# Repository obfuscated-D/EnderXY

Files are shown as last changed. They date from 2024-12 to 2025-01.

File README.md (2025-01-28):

# Ender3XY Conversion

# NOTE: I will be adding more information and resources as I go.All the files and designs are here but assembly instructions are not finished. Unfortunately I don't have as much free time as I did when I started this project.

<p align="center">
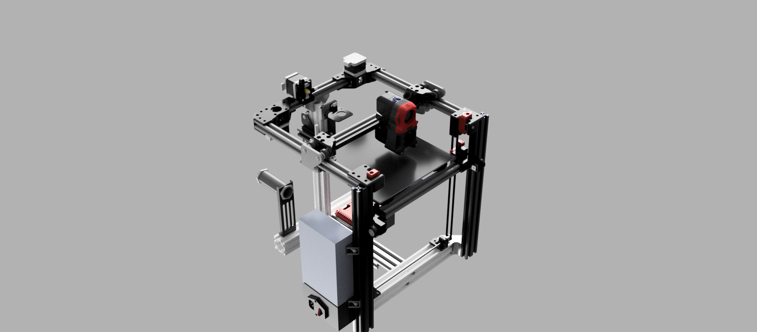
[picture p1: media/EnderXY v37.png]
enderxy

</p>

## Please Read Everything Below Before Contributing, Commenting, or Opening Issues, Thank You!
### This isn't a finished product / refined design. This was a *very* quick concept build and could absolutely use improvement. I hope it can serve as a decent starting point.

# Disclaimer
This project is not affiliated with Creality, Voron Design, Marlin, Mainsail, Klipper, or any other company or project. This is a personal project, and is not intended to be sold or distributed for profit. This project is provided as-is, and I am not responsible for any damage to your printer, or any other equipment. Please accept that when you start this conversion, you cannot change the printer back to stock. By using this project, you agree to take full responsibility for any damage or injury that may occur.

## Skill Level
This project is not for beginners. You should have a good understanding of 3D printing, and be comfortable with modifying and assembling a 3D printer (including drilling, cutting and tapping metal, soldering, etc.). You should also be comfortable with flashing firmware, and configuring it.

# Ender3XY
This is a project to convert a Creality Ender 3 into a CoreXY printer. The goal is to make a good, fast printer from a cheap, slow printer.
- [Contributing](#contributing)
- [TODO's and notes](#todos-and-notes)
- [Klipper](#klipper)
- [Marlin](#marlin)
# Goals
- Make a good printer from a cheap printer
- Keep part cost under $50usd for the conversion
- Use as many stock parts as possible
- Make it easily upgradeable
- Make it easily printable
- Make it easily assembled
- Make it easily sourced

## Print specs
So far, on the bone stock conversion, I can reliably print very good quality at 10k acceleration, and around 120mm/s with a .2 layer height. The mk8 extruder really maxes out around 10mm/s^3.

## Specs
Build volume (X,Y,Z):

 200,185,200           

## Cost
This will vary wildly with person and location. It's reasonable to assume you can get all the necessary parts for the basic stock conversion (not including the printer), for about $60usd. You'll use a good bit of filament as well.

### The Design
The gantry is an adaptation of a [Voron Trident](https://www.vorondesign.com/voron_trident). Of course, the linear rail version is better, but the V wheel version keeps the cost down, and works great! If you build the v wheel version, you can easily change over to the linear rail version in the future without any modification to the frame or belts. Just attach the rails and swap out the X beam ends.

### The Tool Head
I went with an Afterburner Bowden setup. You can use the afterburner, stealthburner, or dragon burner. The files in here allow you to use the stock ender3 hotend in the afterburner, with a 5015 cooling fan. The 5015 fan upgrade is a must for printing PLA fast. The files for the 5015 fan mod are from [Greg191134](https://github.com/Greg191134/Voron/tree/master/Afterburner%20Optimisation/5015%20fan%20mod).

### Filament Feed
Bowden feed is not the greatest, and is a limiting factor as far as print quality and speed are concerned. The upside of running the Bowden is it greatly decreases the mass fo the gantry. If using the stock motors, this is important! Direct drive would be much better, but wouldn't be worth it without A/B motor upgrades. 

## Marlin Firmware
YOU MAY NEED TO ADJUST SOME OF THE CONFIGURATION !!
In the firmware directory, you will find two .bin files.One for the stm32 and one for the gd32f.  These reflect the configurations found in the marlin configuration files directory. These will only work for:
- Ender3 4.2.2 mainboard with A4988 drivers and stm32 processor
- Ender3 4.2.2 mainboard with A4988 drivers and gd32f processor

### If your board does not match, THE FIRMWARE WILL NOT WORK FOR YOU!
 You need to identify your board and stepper drivers, adjust the configuration files for your build, and build a marlin image. The configuration files needed for marlin 2.x bugfix are in the Marlin_files directory. See [Marlin](https://github.com/MarlinFirmware/Marlin) for more information on how to build your own firmware.

# Klipper
For around $22usd, you can get a raspberry pi zero 2W, and run mainsail with klipper! The Klipper directory has the printer.cfg file for the EnderXY, based on the 4.2.2 mainboard. See [Klipper](https://github.com/Klipper3d/klipper/tree/master) for more info and setup instructions.

# Contributing
I would love to see this project grow, and I would love to see what others can do with it. If you have any ideas, improvements, or requests, please feel free to open an issue, or, fork the project and make a pull request.

# Before you Contribute, Please Read!
### It's easy to just throw money at this, to add better parts and make it a better printer. That's not the point of this project, and it's what makes it a challenge. The point is to make a good printer from a cheap printer, using as many stock parts as possible.
### If you have a suggestion, please consider the cost and the availability of the parts. If you have a design change, please consider the ease of printing and the ease of assembly.
### If you have a request, please consider the goals of the project, and the limitations of the stock parts.

## TODO's and notes
    - optmize part designs for printing without support

# Sources and mentions
The only reason this project was possible, and frankly, why I was able to create the first concept so quickly, is because of awesome open source projects! I don't want anyone to think that I did something amazing here, I simply adapted what I could from others, and made a few parts that weren't out there yet.

Of course [Voron Design](https://vorondesign.com/). An amazing, very generous engineering team.

[Marlin](https://github.com/MarlinFirmware/Marlin), Making the maker world a better place.

This wonderful person [Greg191134](https://github.com/Greg191134) is the source of the 5015 fan mod for the afterburner: [Afterburner 5015 fan mod](https://github.com/Greg191134/Voron/tree/master/Afterburner%20Optimisation/5015%20fan%20mod). They also have an awesome project called the Vorender-4, where they upcycled an ender 4 with an adaptation of the Trident gantry.

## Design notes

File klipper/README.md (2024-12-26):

# Klipper

### The printer.cfg in has been tested with Ender3 4.2.2 mainboard, with the stm32 and gd32f chipsets. 

### There is no guarantee that it will work for you! You may need to modify the printer.cfg once up and running.
### See the [Mainsail docs](https://docs.mainsail.xyz/) for more info on setting up your printer.

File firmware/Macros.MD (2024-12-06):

# Here are some print start and print end macros. You can add this to Machine Settings in Cura
```
; EnderXY Custom Start G-code
G92 E0 ; Reset Extruder
G28 ; Home all axes
G1 Z2.0 F3000 ; Move Z up
G1 X0.1 Y20 Z0.3 F5000.0 ; Move to start position
G1 X0.1 Y150.0 Z0.3 F1500.0 E15 ; Draw the first line
G1 X0.4 Y150.0 Z0.3 F5000.0 ; Move to side a little
G1 X0.4 Y20 Z0.3 F1500.0 E30 ; Draw the second line
G92 E0 ; Reset Extruder
G1 Z2.0 F3000 ; Move Z up
G1 X5 Y20 Z0.3 F5000.0 ; Move over to prevent blob squish
```

```
G91 ;Relative positioning
G1 E-2 F2700 ;Retract a bit
G1 E-2 Z0.2 F2400 ;Retract and raise Z
G1 X5 Y5 F3000 ;Wipe out
G1 Z10 ;Raise Z more
G90 ;Absolute positioning

G1 X0 Y{machine_depth} ;Present print
M106 S0 ;Turn-off fan
M104 S0 ;Turn-off hotend
M140 S0 ;Turn-off bed

M84 X Y E ;Disable all steppers but Z
```

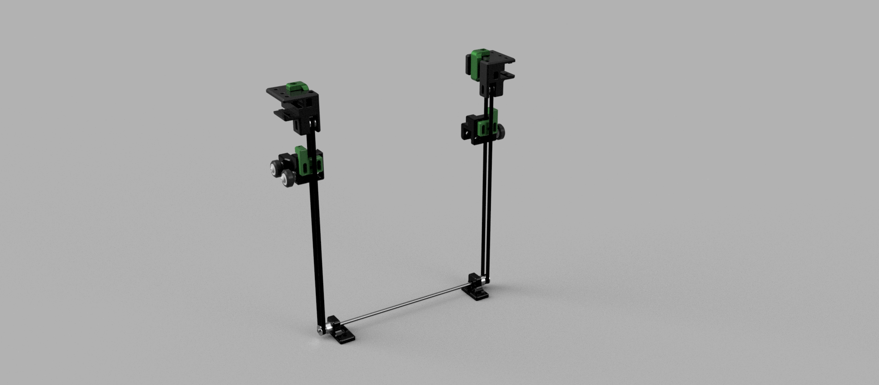
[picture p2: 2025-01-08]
media/Torsion Bar System v7.png

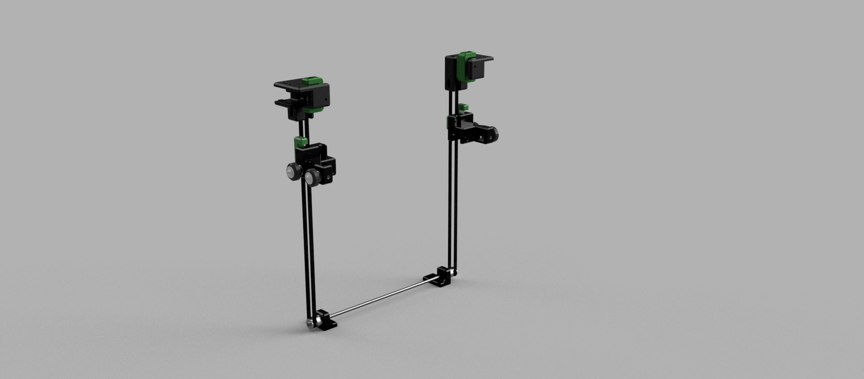
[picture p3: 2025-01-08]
media/Torsion Bar System Front v7.png

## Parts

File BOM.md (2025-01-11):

# The bolt counts are generous, and you may end up with extras
# Extra Components needed to build the EnderXY

        1 Ender-3 printer

## Frame components 
### 20x20 Extrusions:
        1x 196mm
        2x 330mm
        1x 289mm

## Motion Components

        20 F695-2RS Flanged Ball Bearing 5x13x4mm
        
        4 20 Tooth GT2 Idler Pulley, 5mm Bore, 10mm Width 

        2 20 Tooth GT2 Pulley, 5mm Bore, 10mm Width ( 4 if using aftermarket motors!)

        5 meter roll GT2 Timing belt

        250mm mgn12 linear rail (for x axis)
        
        mgn12 linear rail carriage

        300mm 5mm shaft

## Electrical
        For afterburner with 5015 fan:

                1 24V 5015 Blower fan (GDSTIME or SUNON recommended, some cheap fans barely move any air)

        ~5 meters 20 awg wire (for extending the part fan ,motors, and some of the limit switch wires)

        heat shrink for 20 awg wire

## Fasteners

        60 M5x10 BHCS
        
        20 M5x12 BHCS
        
        6 M5x20 BHCS
        
        6 M5x16 BHCS
        
        10 M5x30 BHCS
        
        2 M5x40 BHCS
        
        15 M5x40 SHCS
        
        20 M5 nuts

        30 M5 washers

        100 M5 t-nuts

        8 M3x8 SHCS

        10 M3x12 SHCS

        4 M3x16 BHCS

        4 M3x20 SHCS

        8 M3x25 SHCS

        6 M3x30 SHCS

        8 M3x40 SHCS

        For extrusion with 6mm bolt hole:
                2 M6x20 BHCS 

        For extrusions with 5mm bolt hole:
                2 M5x20 BHCS 

        8  M4 nuts

        16 M3 nuts

        M3x4 heat set inserts (~25)
# Misc
        
        solder
        heat shrink
        zip ties

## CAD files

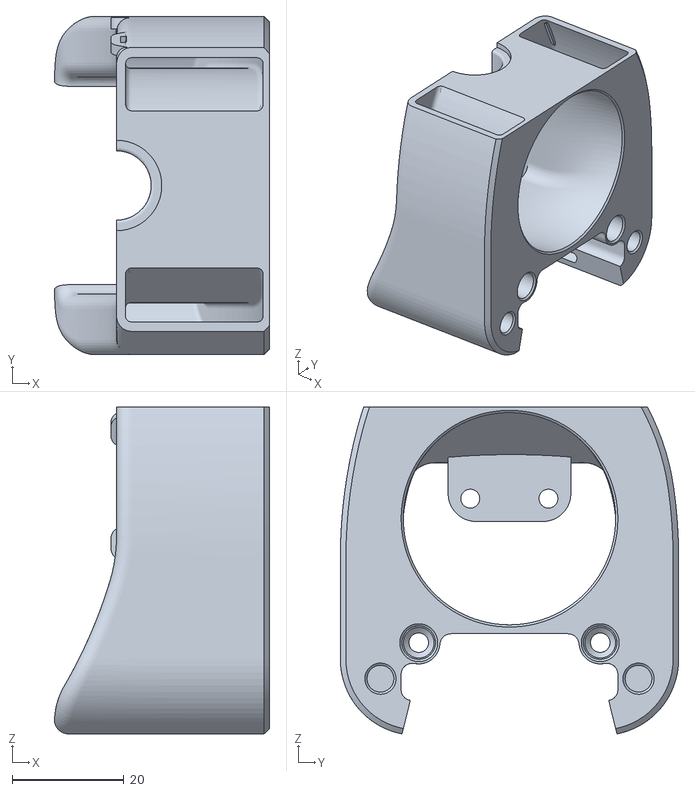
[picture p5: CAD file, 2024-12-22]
STLs/afterburner/mk8-front.stl
38.5 x 60.6 x 58.6

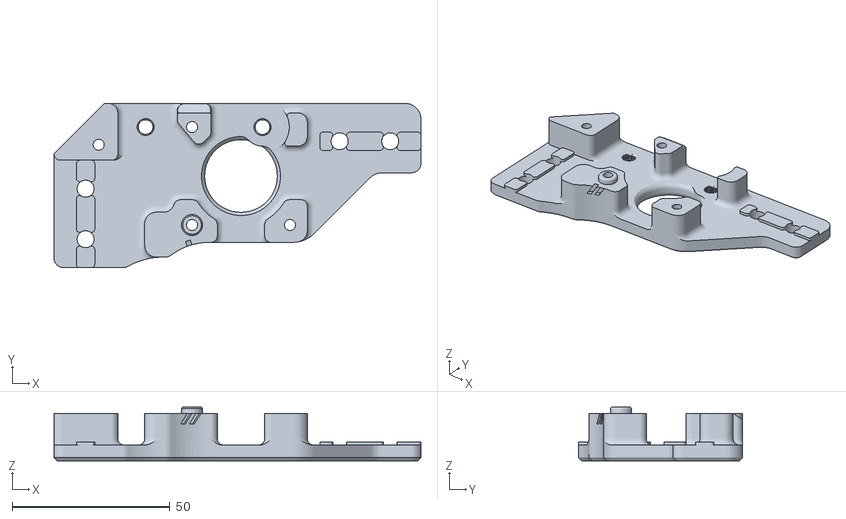
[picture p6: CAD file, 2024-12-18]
STLs/Gantry/Drives/drive_lower_x2.stl
116.2 x 52.0 x 17.0

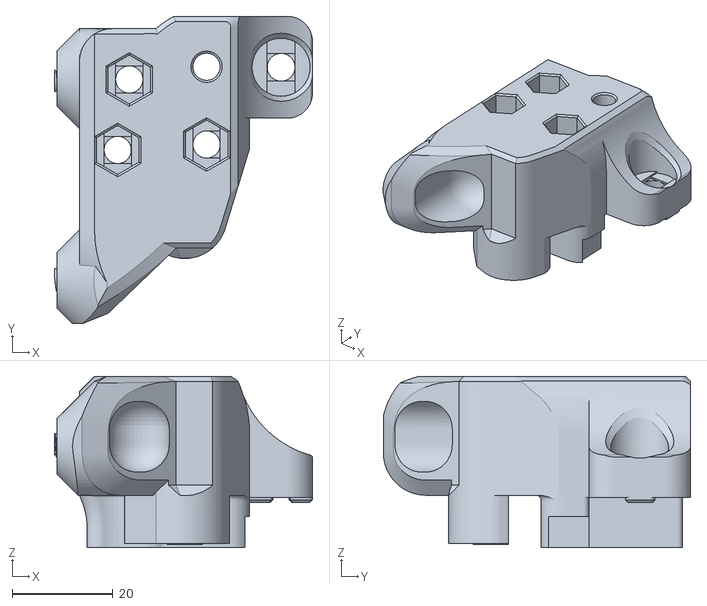
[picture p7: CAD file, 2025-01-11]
STLs/Gantry/x_gantry_end_left_upper_x1.stl
51.2 x 61.0 x 34.0

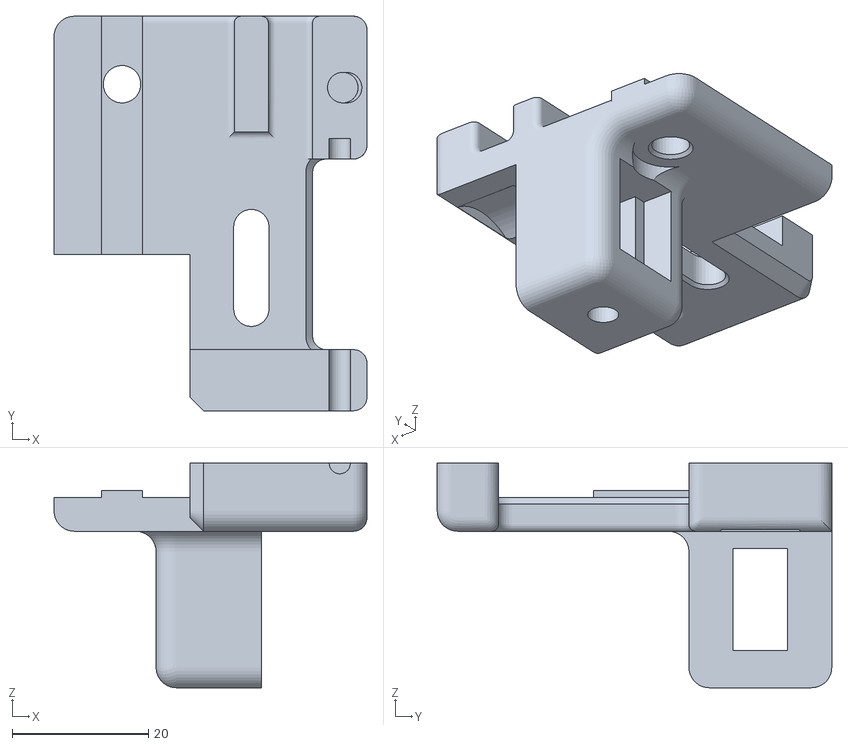
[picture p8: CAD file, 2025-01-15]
STLs/Idlers/idler_b_belted_lower.stl
46.0 x 58.0 x 33.0

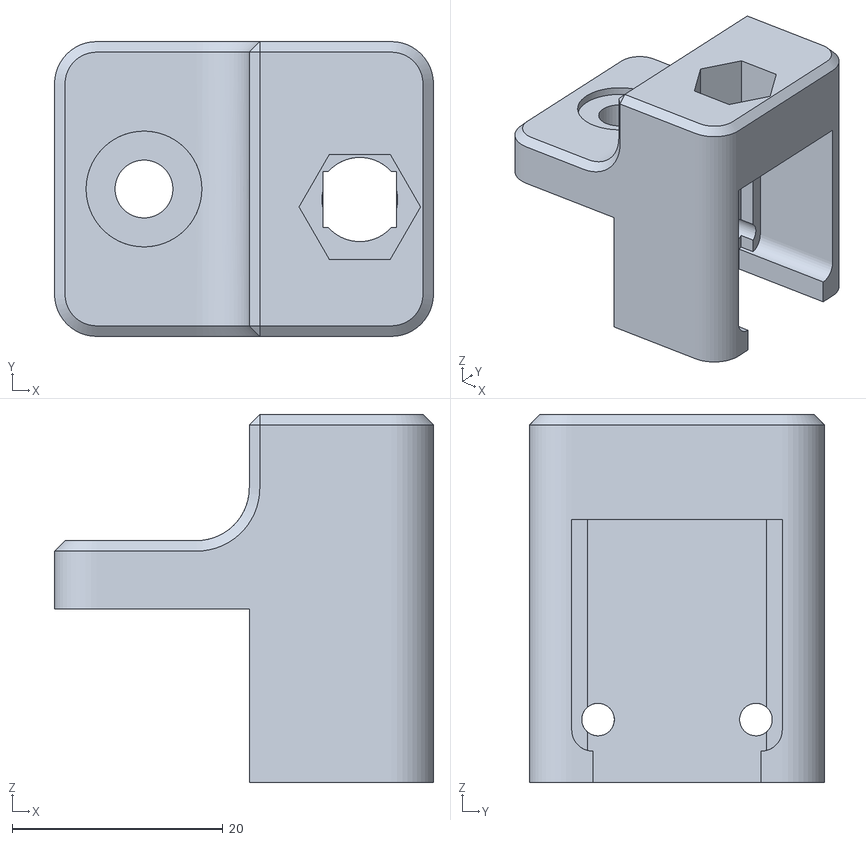
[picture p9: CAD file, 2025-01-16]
STLs/z_endstop_body.stl
36.0 x 28.0 x 35.0

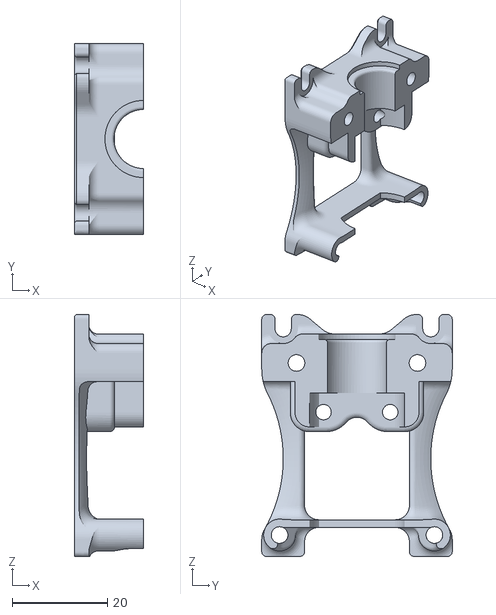
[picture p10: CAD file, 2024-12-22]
STLs/afterburner/mk8-back.stl
14.5 x 40.0 x 50.8

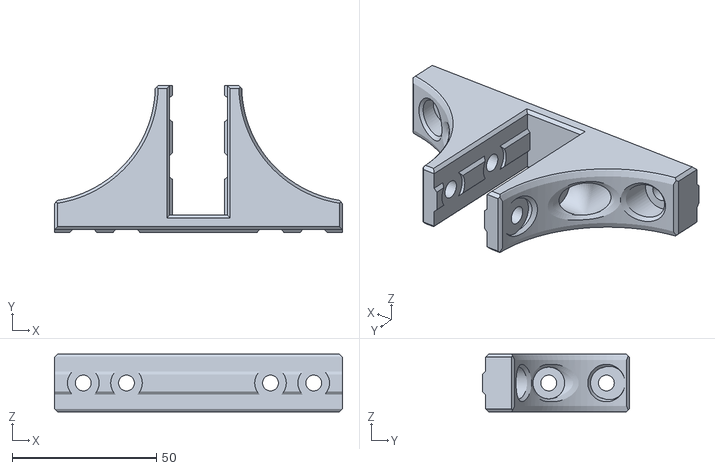
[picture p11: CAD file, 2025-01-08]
STLs/front_support_bracket_x1.stl
100.0 x 51.0 x 20.0

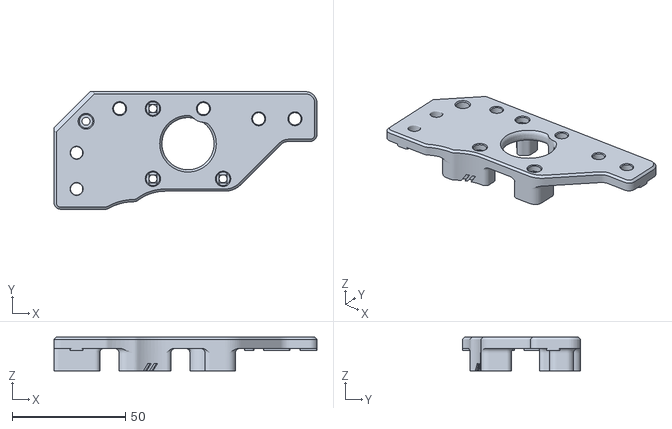
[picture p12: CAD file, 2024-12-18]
STLs/Gantry/Drives/drive_upper_x2.stl
116.2 x 52.0 x 15.0

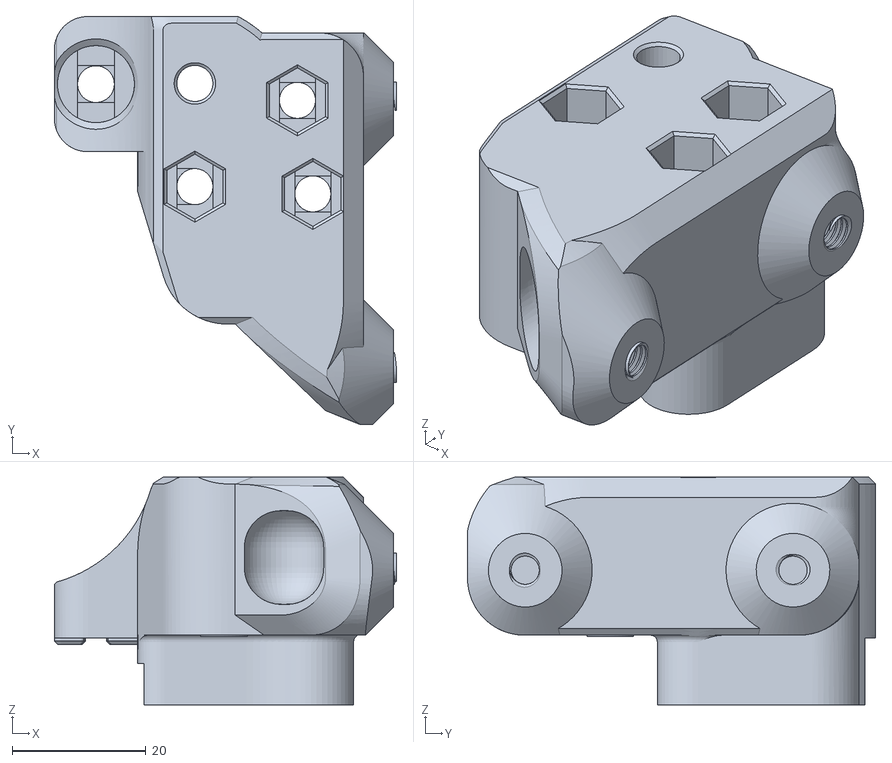
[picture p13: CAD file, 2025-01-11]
STLs/Gantry/x_gantry_end_right_upper_x1.stl
51.2 x 60.9 x 34.0

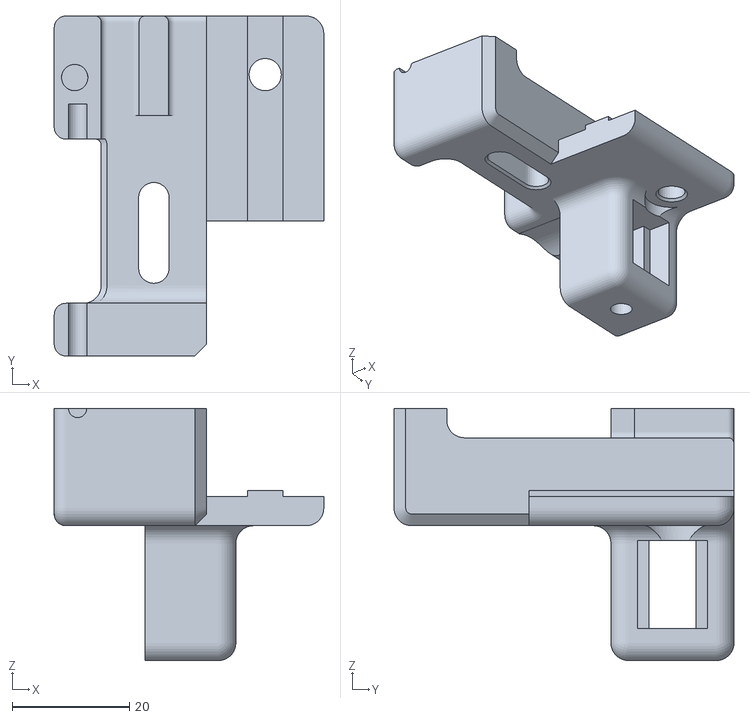
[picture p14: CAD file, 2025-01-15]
STLs/Idlers/ider_a_belted_lower.stl
46.0 x 58.0 x 43.0

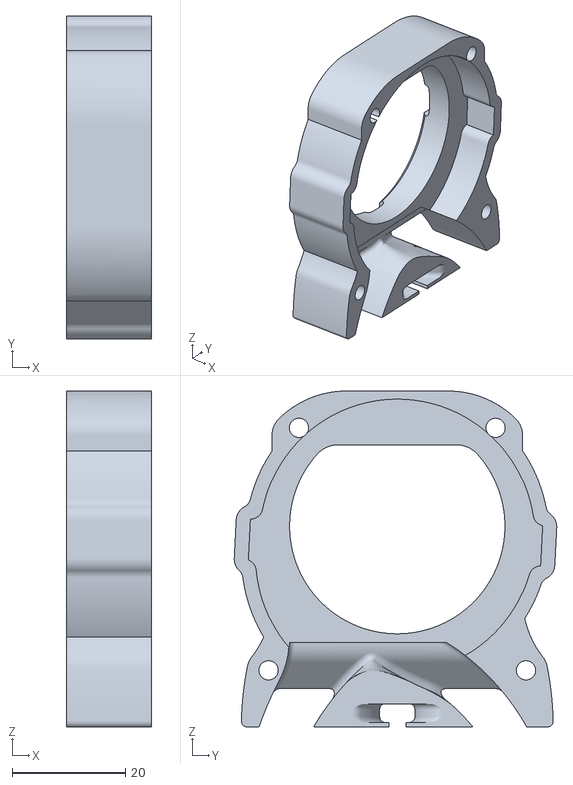
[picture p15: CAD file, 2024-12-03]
STLs/afterburner/5015_mount_back.stl
15.0 x 56.9 x 59.3

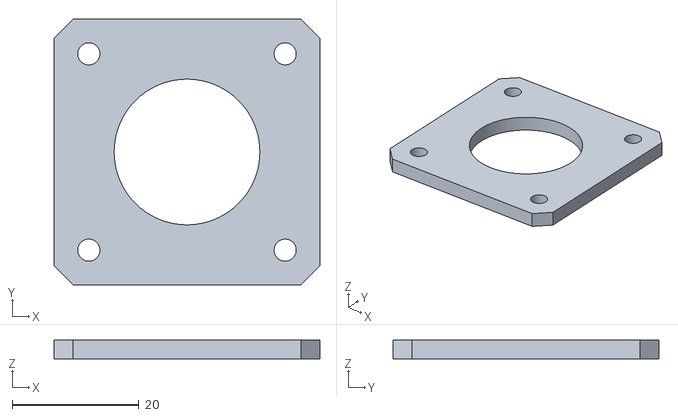
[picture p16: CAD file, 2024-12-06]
STLs/Gantry/Drives/stock_motor_spacer_x2.stl
42.0 x 42.0 x 3.00

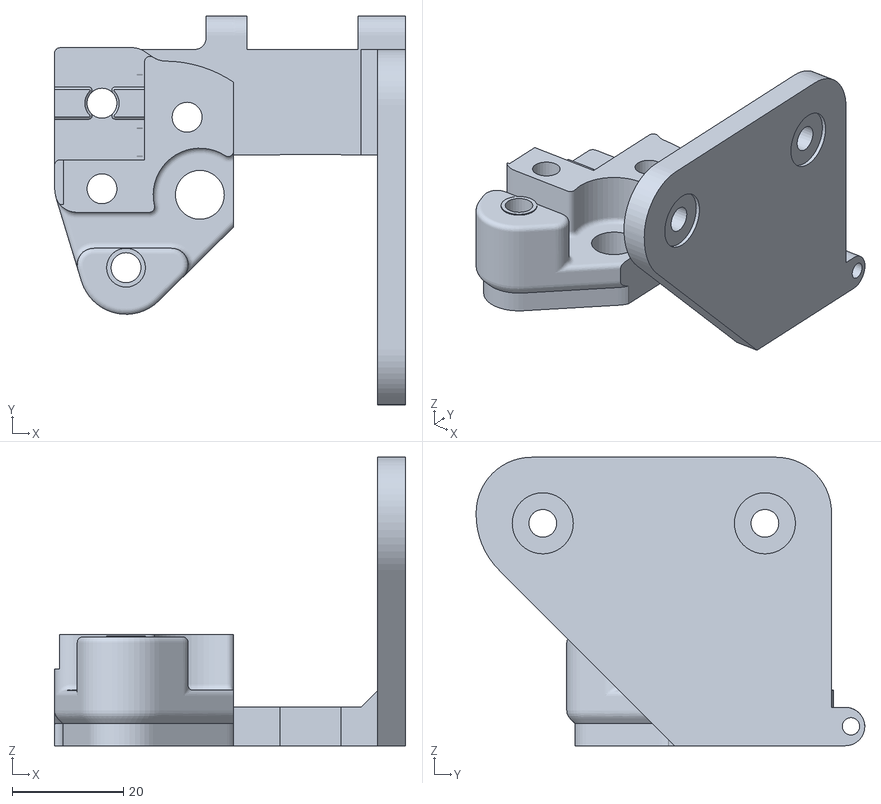
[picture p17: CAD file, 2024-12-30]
STLs/Gantry/x_gantry_end_right_bottom_x1.stl
63.2 x 70.0 x 52.0

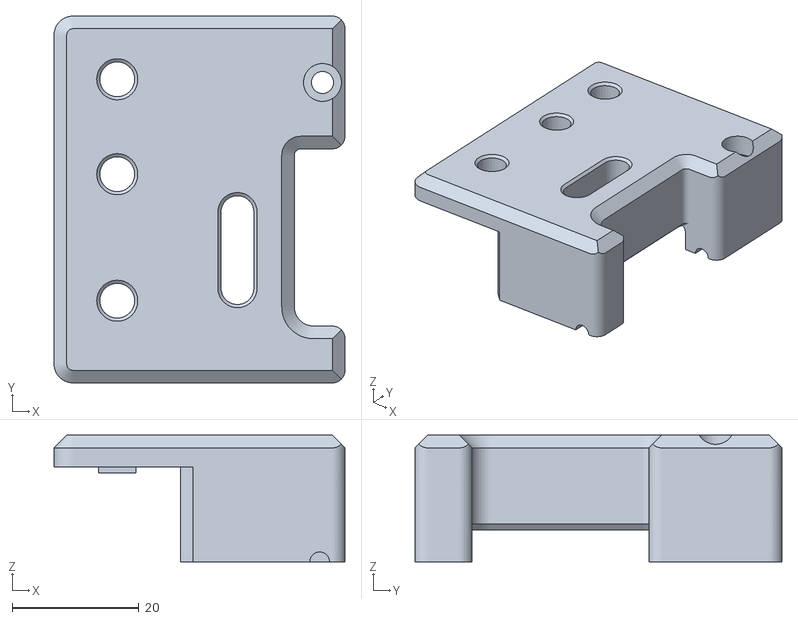
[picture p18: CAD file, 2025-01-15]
STLs/Idlers/idler_b_belted_top.stl
46.0 x 58.0 x 20.0

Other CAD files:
STLs/z_belt_clamp_right_x1.stl
STLs/afterburner/bowden_rear.stl
STLs/Gantry/x_gantry_end_left_bottom_x1.stl
STLs/Gantry/[a]_tensioner_left_x1.stl
STLs/Gantry/[a]_tensioner_right_x1.stl
STLs/Gantry/v_wheel_tensioner_left_x1.stl
STLs/Gantry/v_wheel_tensioner_right_x1.stl
STLs/Gantry/x_carriage_left_x1.stl
STLs/Gantry/x_carriage_right_x1.stl
STLs/Idlers/idler_a_belted_top.stl
STLs/Y_limit_switch_mount_x1.stl
STLs/afterburner/5015_mount_front - Sunon 5015 fan.stl
STLs/afterburner/bowden_single_front.stl
STLs/afterburner/hotend_fan_mount.stl
STLs/bearing_block_left_x1.stl
STLs/bearing_block_right_x1.stl
STLs/electronics_enclosure_bottom.stl
STLs/electronics_enclosure_top.stl
STLs/frame_rear_mount_x1.stl
STLs/front_beam_roller_belted_z_left_x1.stl
STLs/front_beam_roller_belted_z_right_x1.stl
STLs/front_leg_support_left_x1.stl
STLs/front_leg_support_right_x1.stl
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

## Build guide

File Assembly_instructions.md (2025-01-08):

# Required Tools
- Drill (Drill press preferably)
- 5mm (5x.8) tap and appropriate Drill
- 6mm (6x1) tap in some cases and appropriate drill (some available 20mm extrusions have a hole too large for 5mm threads)
- 3mm tap
- Drill
- Drill bit set
- 300mm (12 inch) square
- Allen wrench set (metric)
- Hacksaw (something to cut the extrusions)
- Wiring tools (wire stripper, jst crimpers, wire cutters,etc)
- Soldering Iron
- 3D printer
- Metric ruler and calipers (up to 350mm)
- File
- Sandpaper
- Deburring tool or hobby knife
- Side cutters

## Printing parts:
### Settings:
- ABS or ASA is recommended, but PETG will work (components near the bed and hotend may warp over time if using PETG)
- 0.4mm nozzle
- 0.2mm layer height
- 30% gyroid infill
- 3 perimeters
- 4 top and bottom layers
- Zig Zag support where needed (easier to remove)

- Each component in the STL directory has it's name followed by _x(n), where n is the number of them you need to print. If there is no number, print one.
- Special cases:
    - For the front leg supports, if you are using the stock electronics enclosure, you need to print one left and one right. 
    - If not using the stock enclosure, print 2 lefts

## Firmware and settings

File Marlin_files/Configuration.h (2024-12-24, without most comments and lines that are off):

#pragma once
#define CONFIG_EXAMPLES_DIR "Creality/Ender-3/CrealityV422"
#define CONFIGURATION_H_VERSION 02010300
#define STRING_CONFIG_H_AUTHOR "Obfuscated_D" // Original author or contributor.
  #define MOTHERBOARD BOARD_CREALITY_V422
#define SERIAL_PORT 1
#define BAUDRATE 115200
#define CUSTOM_MACHINE_NAME "EnderXY 0.0.1"
#define X_DRIVER_TYPE  TMC2208_STANDALONE
#define Y_DRIVER_TYPE  TMC2208_STANDALONE
#define Z_DRIVER_TYPE  TMC2208_STANDALONE
#define E0_DRIVER_TYPE TMC2208_STANDALONE
#define EXTRUDERS 1
#define DEFAULT_NOMINAL_FILAMENT_DIA 1.75
#define TEMP_SENSOR_0 1
#define TEMP_SENSOR_1 0
#define TEMP_SENSOR_2 0
#define TEMP_SENSOR_3 0
#define TEMP_SENSOR_4 0
#define TEMP_SENSOR_5 0
#define TEMP_SENSOR_6 0
#define TEMP_SENSOR_7 0
#define TEMP_SENSOR_BED 1
#define TEMP_SENSOR_PROBE 0
#define TEMP_SENSOR_CHAMBER 0
#define TEMP_SENSOR_COOLER 0
#define TEMP_SENSOR_BOARD 0
#define TEMP_SENSOR_SOC 0
#define TEMP_SENSOR_REDUNDANT 0
#define DUMMY_THERMISTOR_998_VALUE  25
#define DUMMY_THERMISTOR_999_VALUE 100
#if TEMP_SENSOR_IS_MAX_TC(0)
  #define MAX31865_SENSOR_OHMS_0      100 // (Ω) Typically 100 or 1000 (PT100 or PT1000)
  #define MAX31865_CALIBRATION_OHMS_0 430 // (Ω) Typically 430 for Adafruit PT100; 4300 for Adafruit PT1000
#endif
#if TEMP_SENSOR_IS_MAX_TC(1)
  #define MAX31865_SENSOR_OHMS_1      100
  #define MAX31865_CALIBRATION_OHMS_1 430
#endif
#if TEMP_SENSOR_IS_MAX_TC(2)
  #define MAX31865_SENSOR_OHMS_2      100
  #define MAX31865_CALIBRATION_OHMS_2 430
#endif
#if HAS_E_TEMP_SENSOR
  #define TEMP_RESIDENCY_TIME         10  // (seconds) Time to wait for hotend to "settle" in M109
  #define TEMP_WINDOW                  1  // (°C) Temperature proximity for the "temperature reached" timer
  #define TEMP_HYSTERESIS              3  // (°C) Temperature proximity considered "close enough" to the target
#endif
#if TEMP_SENSOR_BED
  #define TEMP_BED_RESIDENCY_TIME     10  // (seconds) Time to wait for bed to "settle" in M190
  #define TEMP_BED_WINDOW              1  // (°C) Temperature proximity for the "temperature reached" timer
  #define TEMP_BED_HYSTERESIS          3  // (°C) Temperature proximity considered "close enough" to the target
#endif
#if TEMP_SENSOR_CHAMBER
  #define TEMP_CHAMBER_RESIDENCY_TIME 10  // (seconds) Time to wait for chamber to "settle" in M191
  #define TEMP_CHAMBER_WINDOW          1  // (°C) Temperature proximity for the "temperature reached" timer
  #define TEMP_CHAMBER_HYSTERESIS      3  // (°C) Temperature proximity considered "close enough" to the target
#endif
#if TEMP_SENSOR_REDUNDANT
  #define TEMP_SENSOR_REDUNDANT_SOURCE    E1  // The sensor that will provide the redundant reading.
  #define TEMP_SENSOR_REDUNDANT_TARGET    E0  // The sensor that we are providing a redundant reading for.
  #define TEMP_SENSOR_REDUNDANT_MAX_DIFF  10  // (°C) Temperature difference that will trigger a print abort.
#endif
#define HEATER_0_MINTEMP   5
#define HEATER_1_MINTEMP   5
#define HEATER_2_MINTEMP   5
#define HEATER_3_MINTEMP   5
#define HEATER_4_MINTEMP   5
#define HEATER_5_MINTEMP   5
#define HEATER_6_MINTEMP   5
#define HEATER_7_MINTEMP   5
#define BED_MINTEMP        5
#define CHAMBER_MINTEMP    5
#define HEATER_0_MAXTEMP 275
#define HEATER_1_MAXTEMP 275
#define HEATER_2_MAXTEMP 275
#define HEATER_3_MAXTEMP 275
#define HEATER_4_MAXTEMP 275
#define HEATER_5_MAXTEMP 275
#define HEATER_6_MAXTEMP 275
#define HEATER_7_MAXTEMP 275
#define BED_MAXTEMP      125
#define CHAMBER_MAXTEMP  60
#define HOTEND_OVERSHOOT 15   // (°C) Forbid temperatures over MAXTEMP - OVERSHOOT
#define BED_OVERSHOOT    10   // (°C) Forbid temperatures over MAXTEMP - OVERSHOOT
#define COOLER_OVERSHOOT  2   // (°C) Forbid temperatures closer than OVERSHOOT
#define PIDTEMP           // See the PID Tuning Guide at https://reprap.org/wiki/PID_Tuning
#define PID_MAX  255      // Limit hotend current while PID is active (see PID_FUNCTIONAL_RANGE below); 255=full current
#define PID_K1     0.95   // Smoothing factor within any PID loop
    #define DEFAULT_Kp  21.73
    #define DEFAULT_Ki   1.54
    #define DEFAULT_Kd  76.55
#define MAX_BED_POWER 255 // limits duty cycle to bed; 255=full current
#define MAX_CHAMBER_POWER 255 // limits duty cycle to chamber heater; 255=full current
  #define PID_FUNCTIONAL_RANGE 10 // If the temperature difference between the target temperature and the actual temperature
  #define PID_EDIT_MENU           // Add PID editing to the "Advanced Settings" menu. (~700 bytes of flash)
  #define PID_AUTOTUNE_MENU       // Add PID auto-tuning to the "Advanced Settings" menu. (~250 bytes of flash)
#define PREVENT_COLD_EXTRUSION
#define EXTRUDE_MINTEMP 170
#define PREVENT_LENGTHY_EXTRUDE
#define EXTRUDE_MAXLENGTH 200
#define THERMAL_PROTECTION_HOTENDS // Enable thermal protection for all extruders
#define THERMAL_PROTECTION_BED     // Enable thermal protection for the heated bed
#define THERMAL_PROTECTION_CHAMBER // Enable thermal protection for the heated chamber
#define THERMAL_PROTECTION_COOLER  // Enable thermal protection for the laser cooling
#define COREXY
#define ENDSTOPPULLUPS
#define X_MIN_ENDSTOP_HIT_STATE HIGH
#define X_MAX_ENDSTOP_HIT_STATE HIGH
#define Y_MIN_ENDSTOP_HIT_STATE HIGH
#define Y_MAX_ENDSTOP_HIT_STATE HIGH
#define Z_MIN_ENDSTOP_HIT_STATE HIGH
#define Z_MAX_ENDSTOP_HIT_STATE HIGH
#define I_MIN_ENDSTOP_HIT_STATE HIGH
#define I_MAX_ENDSTOP_HIT_STATE HIGH
#define J_MIN_ENDSTOP_HIT_STATE HIGH
#define J_MAX_ENDSTOP_HIT_STATE HIGH
#define K_MIN_ENDSTOP_HIT_STATE HIGH
#define K_MAX_ENDSTOP_HIT_STATE HIGH
#define U_MIN_ENDSTOP_HIT_STATE HIGH
#define U_MAX_ENDSTOP_HIT_STATE HIGH
#define V_MIN_ENDSTOP_HIT_STATE HIGH
#define V_MAX_ENDSTOP_HIT_STATE HIGH
#define W_MIN_ENDSTOP_HIT_STATE HIGH
#define W_MAX_ENDSTOP_HIT_STATE HIGH
#define Z_MIN_PROBE_ENDSTOP_HIT_STATE HIGH
#define DEFAULT_AXIS_STEPS_PER_UNIT   { 80, 80, 400, 93 }
#define EDITABLE_STEPS_PER_UNIT
#define DEFAULT_MAX_FEEDRATE          { 500, 500, 5, 40 }
#define DEFAULT_MAX_ACCELERATION      { 5000, 5000, 100, 5000 }
#define DEFAULT_ACCELERATION           2500    // X, Y, Z and E acceleration for printing moves
#define DEFAULT_RETRACT_ACCELERATION   500    // E acceleration for retracts
#define DEFAULT_TRAVEL_ACCELERATION    1500    // X, Y, Z acceleration for travel (non printing) moves
  #define JUNCTION_DEVIATION_MM 0.08  // (mm) Distance from real junction edge
  #define JD_HANDLE_SMALL_SEGMENTS    // Use curvature estimation instead of just the junction angle
#define Z_MIN_PROBE_USES_Z_MIN_ENDSTOP_PIN
#define NOZZLE_TO_PROBE_OFFSET { 10, 10, 0 }
#define PROBING_TOOL 0
#define PROBING_MARGIN 10
#define XY_PROBE_FEEDRATE (133*60)
#define Z_PROBE_FEEDRATE_FAST (4*60)
#define Z_PROBE_FEEDRATE_SLOW (Z_PROBE_FEEDRATE_FAST / 2)
#define Z_CLEARANCE_DEPLOY_PROBE   10 // (mm) Z Clearance for Deploy/Stow
#define Z_CLEARANCE_BETWEEN_PROBES  5 // (mm) Z Clearance between probe points
#define Z_CLEARANCE_MULTI_PROBE     5 // (mm) Z Clearance between multiple probes
#define Z_PROBE_ERROR_TOLERANCE     3 // (mm) Tolerance for early trigger (<= -probe.offset.z + ZPET)
#define Z_PROBE_LOW_POINT          -2 // (mm) Farthest distance below the trigger-point to go before stopping
#define X_ENABLE_ON LOW
#define Y_ENABLE_ON LOW
#define Z_ENABLE_ON LOW
#define E_ENABLE_ON LOW // For all extruders
#define INVERT_X_DIR true
#define INVERT_Y_DIR true
#define INVERT_Z_DIR false
#define INVERT_E0_DIR false
#define INVERT_E1_DIR false
#define INVERT_E2_DIR false
#define INVERT_E3_DIR false
#define INVERT_E4_DIR false
#define INVERT_E5_DIR false
#define INVERT_E6_DIR false
#define INVERT_E7_DIR false
#define X_HOME_DIR -1
#define Y_HOME_DIR 1
#define Z_HOME_DIR -1
#define X_BED_SIZE 200
#define Y_BED_SIZE 180
#define X_MIN_POS 0
#define Y_MIN_POS 0
#define Z_MIN_POS 0
#define X_MAX_POS X_BED_SIZE
#define Y_MAX_POS Y_BED_SIZE + 5
#define Z_MAX_POS 200
#define MIN_SOFTWARE_ENDSTOPS
  #define MIN_SOFTWARE_ENDSTOP_X
  #define MIN_SOFTWARE_ENDSTOP_Y
  #define MIN_SOFTWARE_ENDSTOP_Z
  #define MIN_SOFTWARE_ENDSTOP_I
  #define MIN_SOFTWARE_ENDSTOP_J
  #define MIN_SOFTWARE_ENDSTOP_K
  #define MIN_SOFTWARE_ENDSTOP_U
  #define MIN_SOFTWARE_ENDSTOP_V
  #define MIN_SOFTWARE_ENDSTOP_W
#define MAX_SOFTWARE_ENDSTOPS
  #define MAX_SOFTWARE_ENDSTOP_X
  #define MAX_SOFTWARE_ENDSTOP_Y
  #define MAX_SOFTWARE_ENDSTOP_Z
  #define MAX_SOFTWARE_ENDSTOP_I
  #define MAX_SOFTWARE_ENDSTOP_J
  #define MAX_SOFTWARE_ENDSTOP_K
  #define MAX_SOFTWARE_ENDSTOP_U
  #define MAX_SOFTWARE_ENDSTOP_V
  #define MAX_SOFTWARE_ENDSTOP_W
#define HOMING_FEEDRATE_MM_M { (20*60), (20*60), (4*60) }
#define VALIDATE_HOMING_ENDSTOPS
#define EEPROM_SETTINGS       // Persistent storage with M500 and M501
#define EEPROM_CHITCHAT       // Give feedback on EEPROM commands. Disable to save flash.
#define EEPROM_BOOT_SILENT    // Keep M503 quiet and only give errors during first load
#define HOST_KEEPALIVE_FEATURE        // Disable this if your host doesn't like keepalive messages
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

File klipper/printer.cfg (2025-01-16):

# This file contains pin mappings for the stock 2020 Creality Ender 3
# V2. To use this config, during "make menuconfig" select the
# STM32F103 with a "28KiB bootloader" and serial (on USART1 PA10/PA9)
# communication.

# If you prefer a direct serial connection, in "make menuconfig"
# select "Enable extra low-level configuration options" and select
# serial (on USART3 PB11/PB10), which is broken out on the 10 pin IDC
# cable used for the LCD module as follows:
# 3: Tx, 4: Rx, 9: GND, 10: VCC

# Flash this firmware by copying "out/klipper.bin" to a SD card and
# turning on the printer with the card inserted. The firmware
# filename must end in ".bin" and must not match the last filename
# that was flashed.

# See docs/Config_Reference.md for a description of parameters.

#Uncomment if using mainsail
#[include mainsail.cfg]

[stepper_x]
step_pin: PC2
dir_pin: !PB9
enable_pin: !PC3
microsteps: 16
rotation_distance: 40
endstop_pin: ^PA5
position_endstop: 200
position_max: 200
homing_speed: 50

[stepper_y]
step_pin: PB8
dir_pin: PB7
enable_pin: !PC3
microsteps: 16
rotation_distance: 40
endstop_pin: ^PA6
position_endstop: 180
position_max: 180
homing_speed: 50

[stepper_z]
step_pin: PB6
dir_pin: PB5
enable_pin: !PC3
microsteps: 16
rotation_distance: 8
endstop_pin: ^PA7
position_endstop: -1.5
position_max: 200
position_min: -4

[safe_z_home]
##  XY Location of the Z Endstop Switch, You need to verify and adjust this value!!!!!!!!!!!!!!!!
home_xy_position:93,180
speed:100
z_hop:10

[extruder]
max_extrude_only_distance: 100.0
step_pin: PB4
dir_pin: PB3
enable_pin: !PC3
microsteps: 16
rotation_distance: 34.406
nozzle_diameter: 0.400
filament_diameter: 1.750
heater_pin: PA1
sensor_type: EPCOS 100K B57560G104F
sensor_pin: PC5
control: pid
# tuned for stock hardware with 200 degree Celsius target
pid_Kp: 21.527
pid_Ki: 1.063
pid_Kd: 108.982
min_temp: 0
max_temp: 270

[heater_bed]
heater_pin: PA2
sensor_type: EPCOS 100K B57560G104F
sensor_pin: PC4
control: pid
# tuned for stock hardware with 50 degree Celsius target
pid_Kp: 54.027
pid_Ki: 0.770
pid_Kd: 948.182
min_temp: 0
max_temp: 130

[fan]
pin: PA0

[mcu]
serial: /dev/serial/by-id/usb-1a86_USB_Serial-if00-port0
restart_method: command

[printer]
kinematics: corexy
max_velocity: 300
max_accel: 6000
max_z_velocity: 20
max_z_accel: 100


# Uncomment the following lines to use the factory 12864 LCD display
# [display]
# lcd_type: st7920
# cs_pin: EXP1_7
# sclk_pin: EXP1_6
# sid_pin: EXP1_8
# encoder_pins: ^EXP1_5, ^EXP1_3
# click_pin: ^!EXP1_2



# [board_pins]
# aliases:
#     # EXP1 header
#     EXP1_1=PB5,  EXP1_3=PA9,   EXP1_5=PA10, EXP1_7=PB8,  EXP1_9=<GND>,
#     EXP1_2=PA15, EXP1_4=<RST>, EXP1_6=PB9,  EXP1_8=PB15, EXP1_10=<5V>

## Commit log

2024-12-02 add firmware and config files
    [Configuration.h, Configuration_adv.h]
2024-12-02 add BOM
2024-12-02 update BOM
2024-12-03 README,gitignore, BOM
2024-12-03 readme, afterburner stls
    [5015_mount_back.stl, 5015_mount_front - Sunon 5015 fan.stl, AB_Mk8_Ender5_stock_Back.stl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]
2024-12-03 readme, remove files
    [[a]_blower_housing_front.stl, blower_housing_rear.stl, bowden_single_tl_collet_adapter.stl]
2024-12-04 add first gantry files
2024-12-04 add cad folder, update step file
2024-12-05 remove old mk8 adapter stl
    [AB_Mk8_Ender5_stock_Back.stl]
2024-12-06 updated gantry
    [stock_motor_spacer.stl]
2024-12-18 Stable design files
    [A_Drive_Frame_Lower.stl, A_Drive_Frame_Upper.stl, B_Drive_Frame_Lower.stl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]
2024-12-18 README, Notice
    [[a]_tensioner_left.stl, [a]_tensioner_right.stl, front_idler_a_x2.stl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]
2024-12-20 add files, readme
    [x_carriage_left.stl, x_carriage_right.stl]
2024-12-20 update gantry end lowers
    [x_gantry_left_lower_x1.stl, x_gantry_left_upper_x1.stl, x_gantry_right_lower_x1.stl]
2024-12-22 readme, mk-8 parts
    [mk8-back.stl, mk8-front.stl]
2024-12-24 add photos, new logo, update configuration files
    [Configuration.h]
2024-12-24 new configuration and version files, firmware for gd32
    [Configuration.h]
2024-12-26 add klipper config files, readme
    [printer.cfg]
2024-12-26 new models, readme
    [[a]_tensioner_left.stl, [a]_tensioner_left_x1.stl, [a]_tensioner_right.stl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]
2024-12-26 motor spacer
    [stock_motor_spacer right_x1.stl, stock_motor_spacer_x2.stl]
2024-12-30 Design revision
    [electronics_eclousure_bottom.stl, electronics_enclosure_top.stl, electronics_enclosure_top_pizero2w.stl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]
2024-12-30 Revised electronics enclosure,added linear rail
    [electronics_eclousure_bottom.stl, electronics_enclosure_bottom.stl, electronics_enclosure_top.stl]
2025-01-05 configs, readme
    [printer.cfg]
2025-01-08 add belt system
    [a_idler_belted_bottom.stl, a_idler_belted_top.stl, b_idler_belted_bottom.stl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]
2025-01-08 readme, belt system
    [front_beam_roller_belted_z_left.stl, front_beam_roller_belted_z_right.stl]
2025-01-08 BOM updates
2025-01-08 updated design
    [front_beam_bed_bracket_x1.stl, front_roller_mount_main_body_x2.stl, front_support_bracket.stl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]
2025-01-09 remove old idlers
    [front_idler_a_x2.stl, front_idler_b_x2.stl]
2025-01-11 updated model, hardware
    [x_gantry_end_left_upper.stl, x_gantry_end_right_upper.stl]
2025-01-11 organization, naming
    [a_idler_belted_bottom_x1.stl, a_idler_belted_top_x1.stl, b_idler_belted_bottom_x1.stl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]
2025-01-11 update bolt count
2025-01-15 updated idlers/belt assembly
    [a_idler_belted_bottom_x1.stl, a_idler_belted_top_x1.stl, b_idler_belted_bottom_x1.stl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]
2025-01-16 add safe z to config
    [printer.cfg]
2025-01-16 add printer config, z endstop
    [printer.cfg, z_endstop_body.stl]

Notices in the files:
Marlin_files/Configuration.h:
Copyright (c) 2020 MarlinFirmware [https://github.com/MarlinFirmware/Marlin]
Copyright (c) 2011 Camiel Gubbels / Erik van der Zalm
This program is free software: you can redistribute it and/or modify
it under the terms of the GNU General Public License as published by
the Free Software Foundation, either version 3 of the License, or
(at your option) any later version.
